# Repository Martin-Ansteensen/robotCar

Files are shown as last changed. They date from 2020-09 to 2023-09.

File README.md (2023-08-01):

# robotCar - Still in progress
A remote controlled robot car with a meccanum drivetrain.
The inspiration for this project was taken from the many First Tech Challenge (FTC) robots that use a meccanum wheel drivetrain with position tracking. The components used in FTC robots are quite expensive, and I wanted to design a low-cost version of these robots,

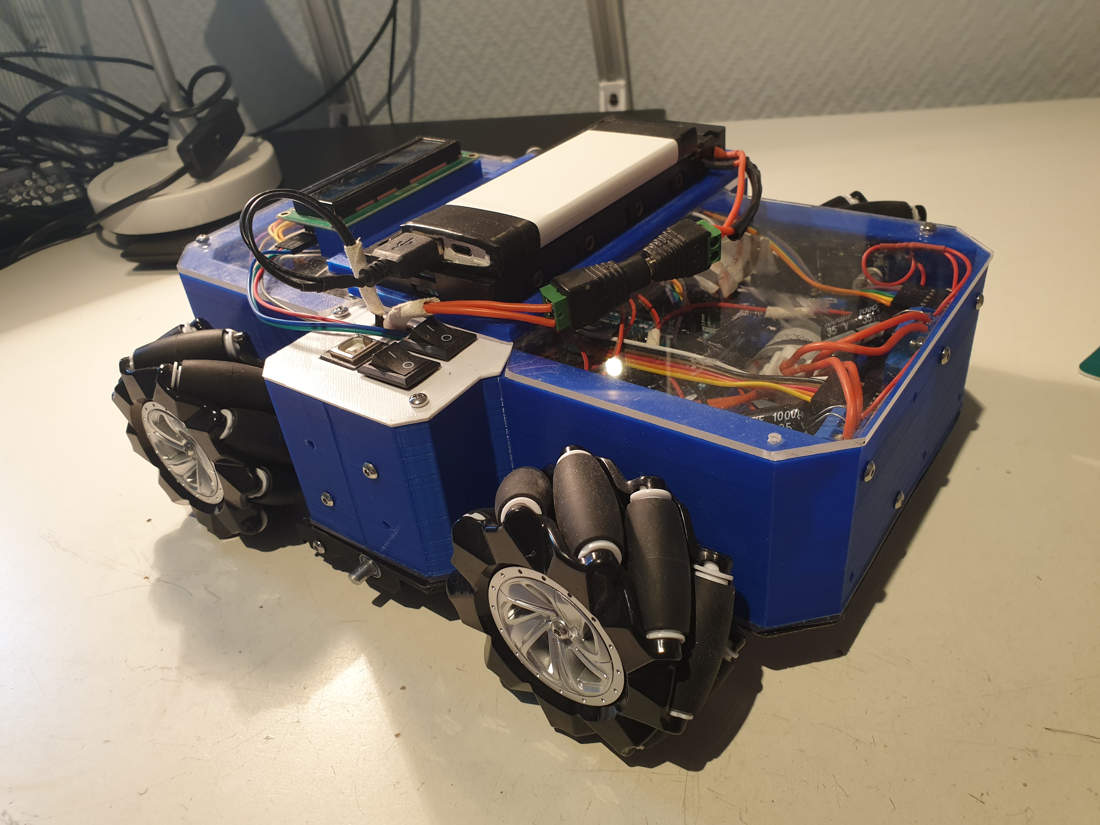
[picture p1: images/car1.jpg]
car


## Objectives
- [x] Meccanum drivetrain that enables the car to drive in all directions.
- [x] Remote control for the car.
- [x] Position tracking system consisting of 3 small omni wheels with encoders.
- [ ] PID-control for each axis of movement (x, y and rotation).
- [ ] Follow a path (predetermined in the program using some sort of a grid), using three omniwheels tracking the movement of the car.

## Design
### Meccanum drivetrain
A meccanum wheel consists of two disks with smaller wheels (rollers) attached in between them. The axis of the rollers are at 45° to the wheel plane and 45° to the axis perpendicular to the disks. A meccanum drivetraing consits of four meccanum wheels, each with it's own DC-motor. By adjusting the speed of each wheel, one can make the drivetrain move in any direction.
### Position tracking (used for odometry)
Tracking the car's position is not easily achieveable as the the meccanum wheels used for the drivetrain slips a lot, which removes the possibilty of using encoders on the drivetrain motors to track the position. Instead, three omni wheels (almost like meccanum wheels, but the axis of the rollers are parallel to the wheel plane), each with it's own rotary encoder is used. To ensure contact with the ground and avoid slipping, the omni wheels were mounted on a small platform with a rubber band forcing them into the ground. By constantly checking the change of the three encoders, the change in the robot's position can be found. 

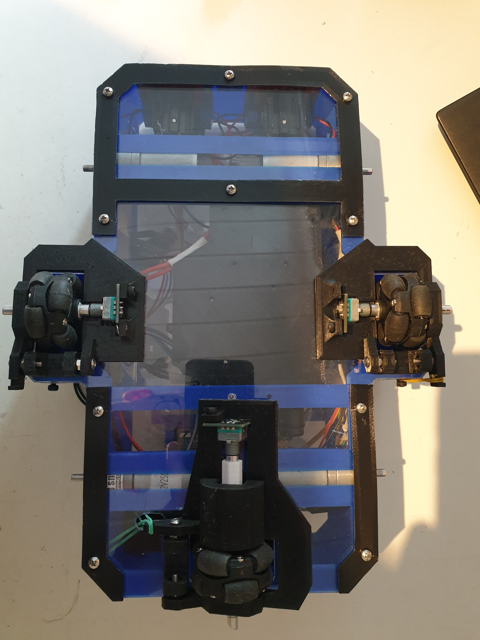
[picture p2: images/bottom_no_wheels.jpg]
bottom_no_wheels

bottom_with_wheels

Demo of the position tracking algorithm. Some error is present, as expected, but it is usable. The error is mainly caused by missed encoder-steps and the encoders low resolution (only 40 steps per revolution), causing accumulative error in the position caclulations.

Position tracking demo (https://www.youtube.com/watch?v=OhbFRzOGtvk)

### Electronics
- Gyro (mpu6050). Experimented with using motion data from the sensor to caculate changes in the position, but the data had to much jitter. Did work to keep track of orientation.
- Arduino Mega (main brain of car).
- Three Arduino Pro Minis (in an effort to detect all steps from the rotary encoder, each encoder was connected to it's own designated Arduino responsible for counting the steps of the encoder).
- Four DC-motors
- Two L298N Motor Drivers
- Battery pack (used by motors)
- Power bank (used by the other electronics to avoid voltage spikes caused by motors)
- Buck converter (transform voltage from power bank)
- LCD (display the position of the robot)
- Four KY-040 Rotary Encoders
- nrf24l01 (radio module)
- A miscellaneous collection of common components (wires, capacitors, switches)

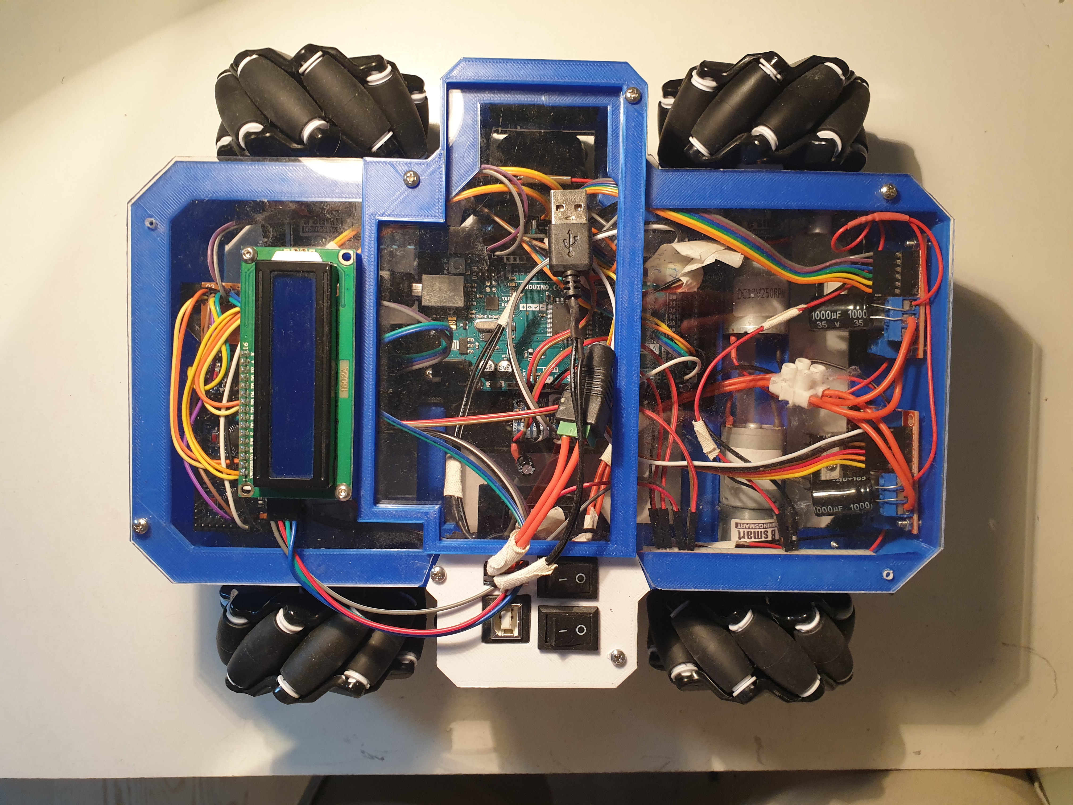
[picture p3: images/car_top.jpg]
car_top


## Remote control
Demo of the car being controlled by a remote control. It is using the position tracking combined with a PID-controller to keep the same orientation.

Remote control demo (https://www.youtube.com/watch?v=tdJjwmVsyyM)

## Path following
The interesting aspect of this project was to make it follow a path (a simple path: drive straight to the left for 10cm, 10cm forward, 10cm diagonally, or a more complex one: a circle, any mathematical curve). By interpolating through the path, using feedback from the position tracking to make sure the car drives to each sub-point on the path, one can ultimately follow any path.

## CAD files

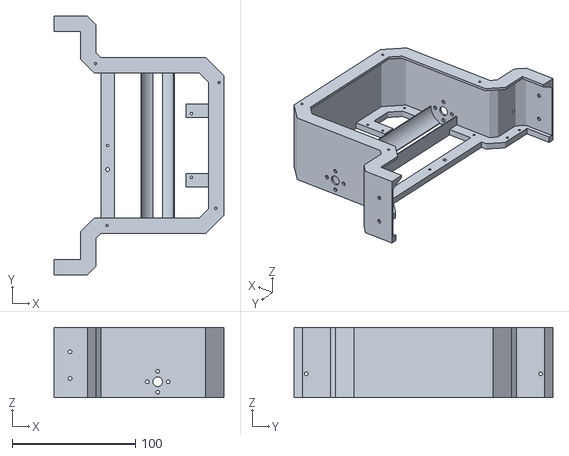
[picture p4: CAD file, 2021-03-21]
3d-model/backBody.stl
137.8 x 210.0 x 57.0

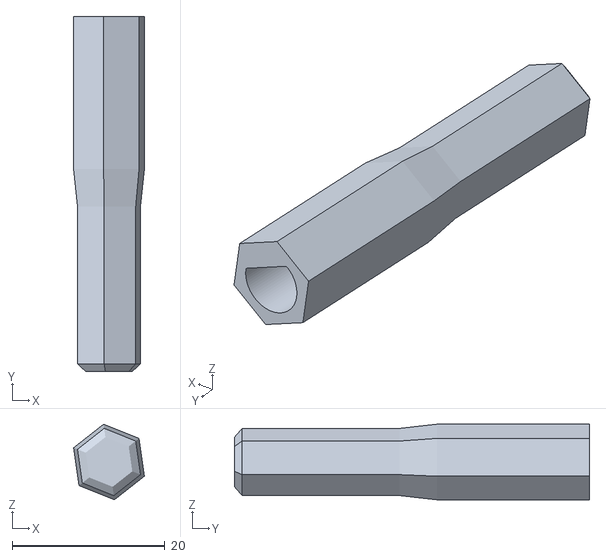
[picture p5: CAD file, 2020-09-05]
couplerLong.stl
9.28 x 46.5 x 9.90

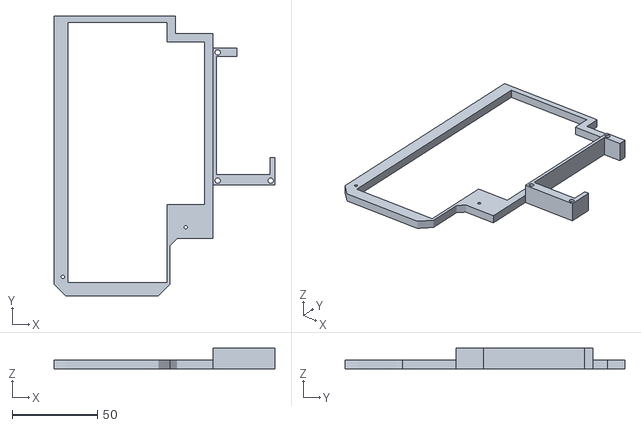
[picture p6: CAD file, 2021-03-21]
3d-model/batteryholder.stl
129.3 x 163.8 x 12.0

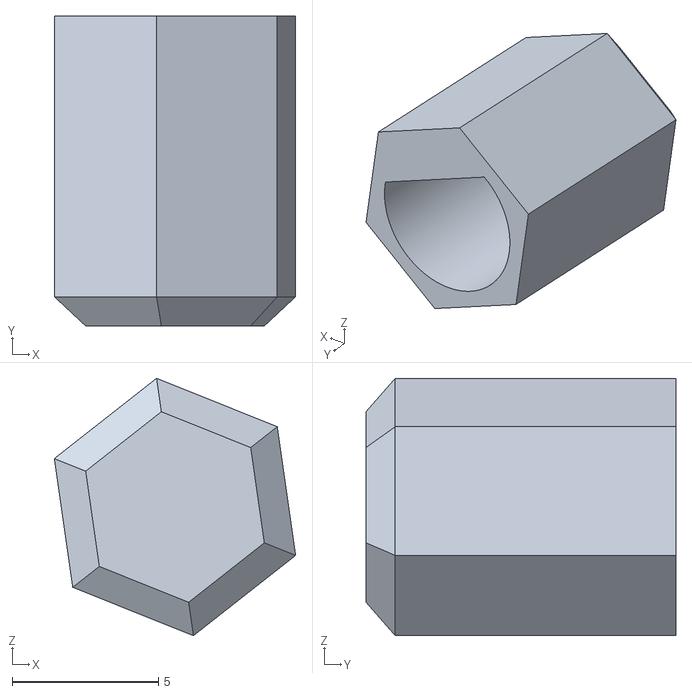
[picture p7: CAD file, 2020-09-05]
smallCoupler.stl
8.25 x 10.6 x 8.80

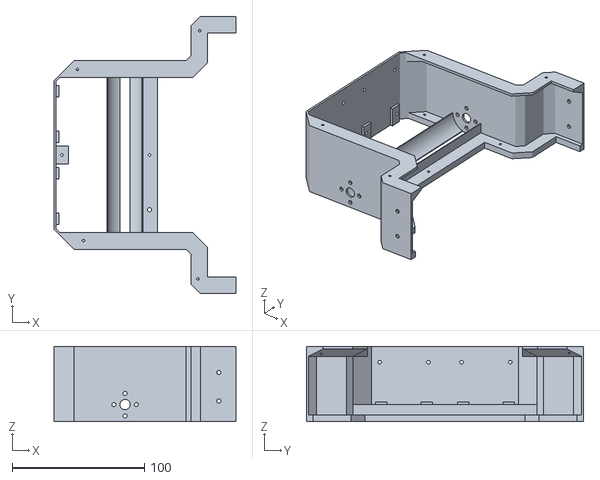
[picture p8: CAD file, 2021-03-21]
3d-model/frontBody.stl
137.8 x 210.0 x 57.0

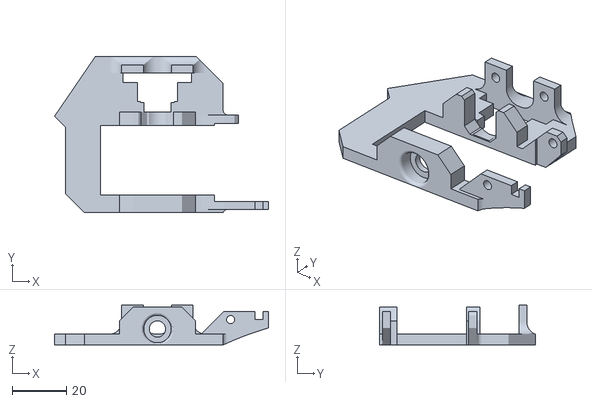
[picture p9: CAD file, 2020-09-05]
LeftOmni.stl
79.0 x 57.7 x 14.8

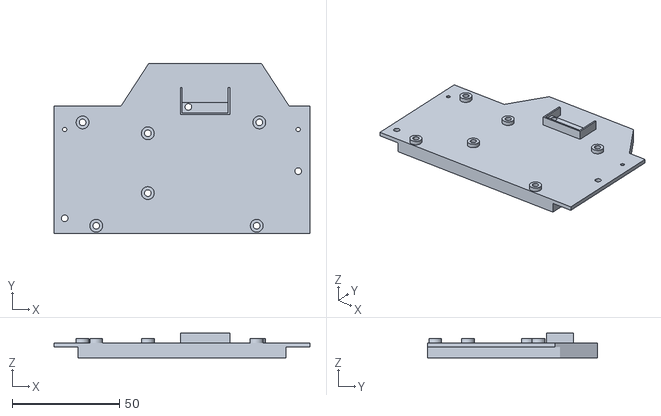
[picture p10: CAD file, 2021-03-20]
3d-model/electronicsplattform.stl
119.5 x 79.1 x 11.5

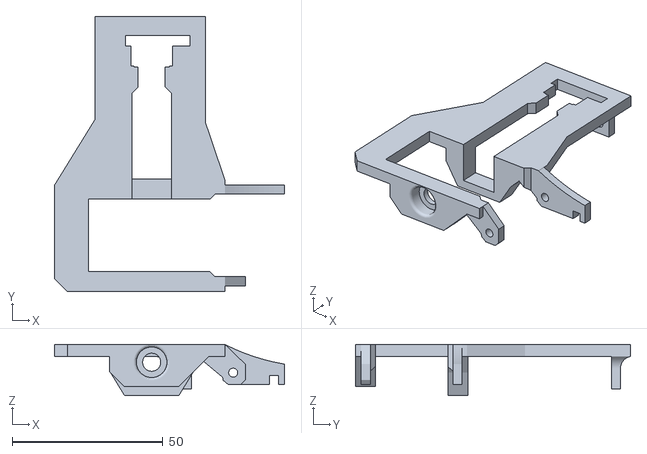
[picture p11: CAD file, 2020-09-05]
BackOmni.stl
76.2 x 91.1 x 16.9

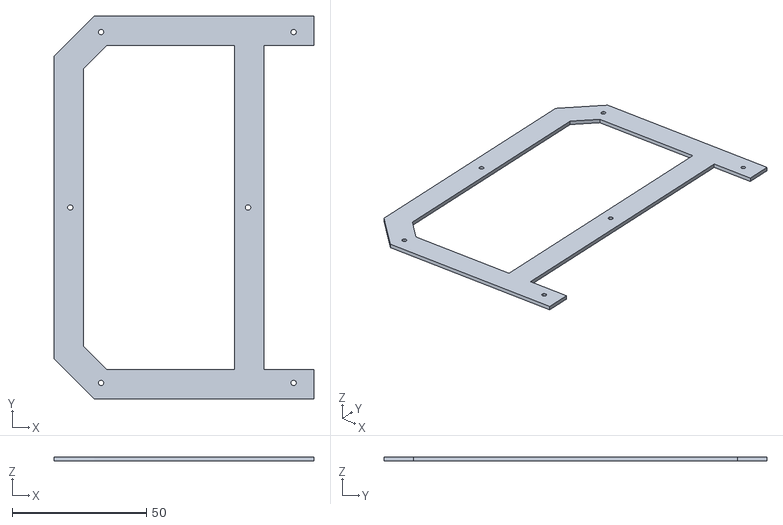
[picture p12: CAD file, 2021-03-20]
3d-model/spacer1.stl
96.8 x 142.8 x 1.60

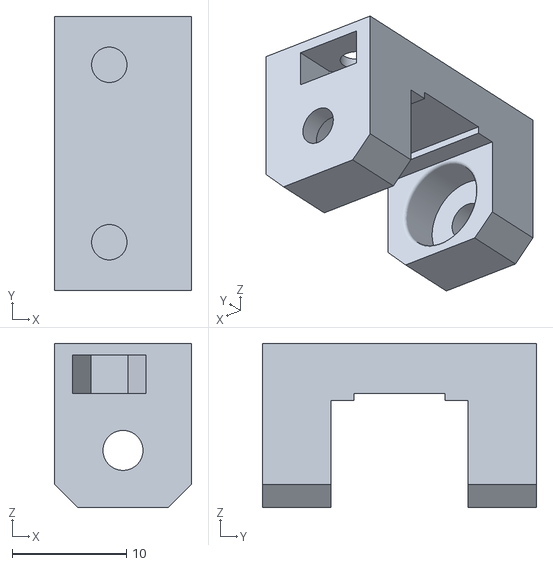
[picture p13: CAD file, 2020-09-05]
3.5Hinge.stl
12.0 x 24.0 x 14.4

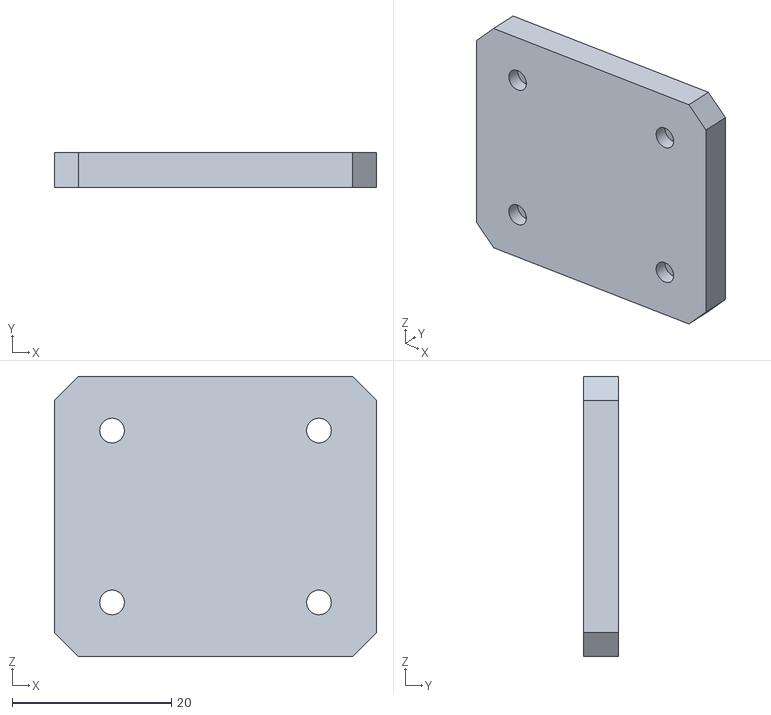
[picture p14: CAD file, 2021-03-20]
3d-model/sideCoupler.stl
40.5 x 4.40 x 35.2

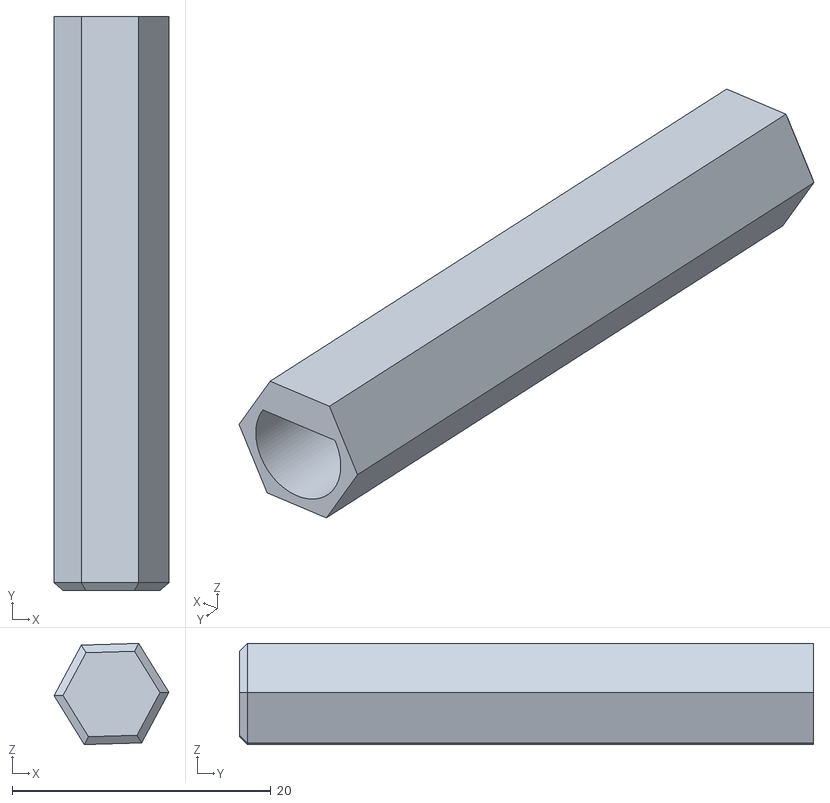
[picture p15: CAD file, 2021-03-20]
3d-model/longcouplr.stl
8.89 x 44.4 x 7.83

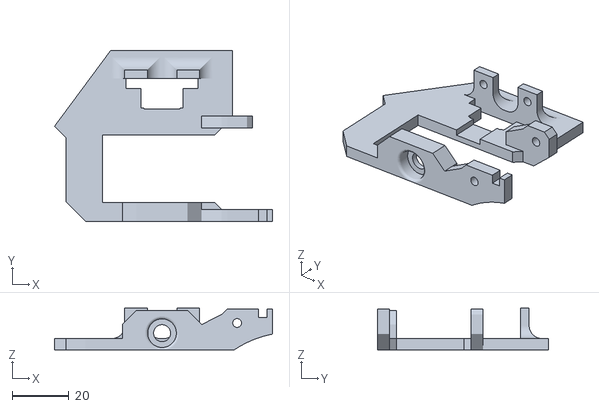
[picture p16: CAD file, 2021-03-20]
3d-model/rightencoder.stl
77.0 x 60.3 x 14.8

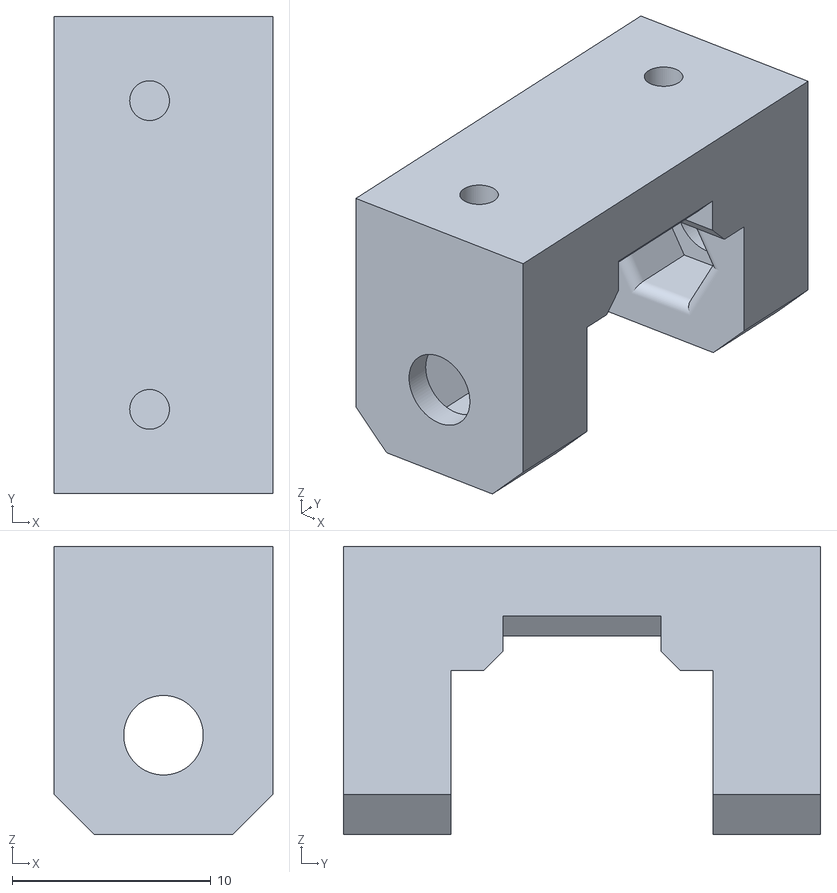
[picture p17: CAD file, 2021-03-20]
3d-model/hinge.stl
11.0 x 24.0 x 14.5

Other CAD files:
RightOmni.stl
3d-model/backencder.stl
3d-model/shortcoupler.stl
3d-model/spacer2.stl
3d-model/leftencoder.stl
3d-model/spacer3.stl

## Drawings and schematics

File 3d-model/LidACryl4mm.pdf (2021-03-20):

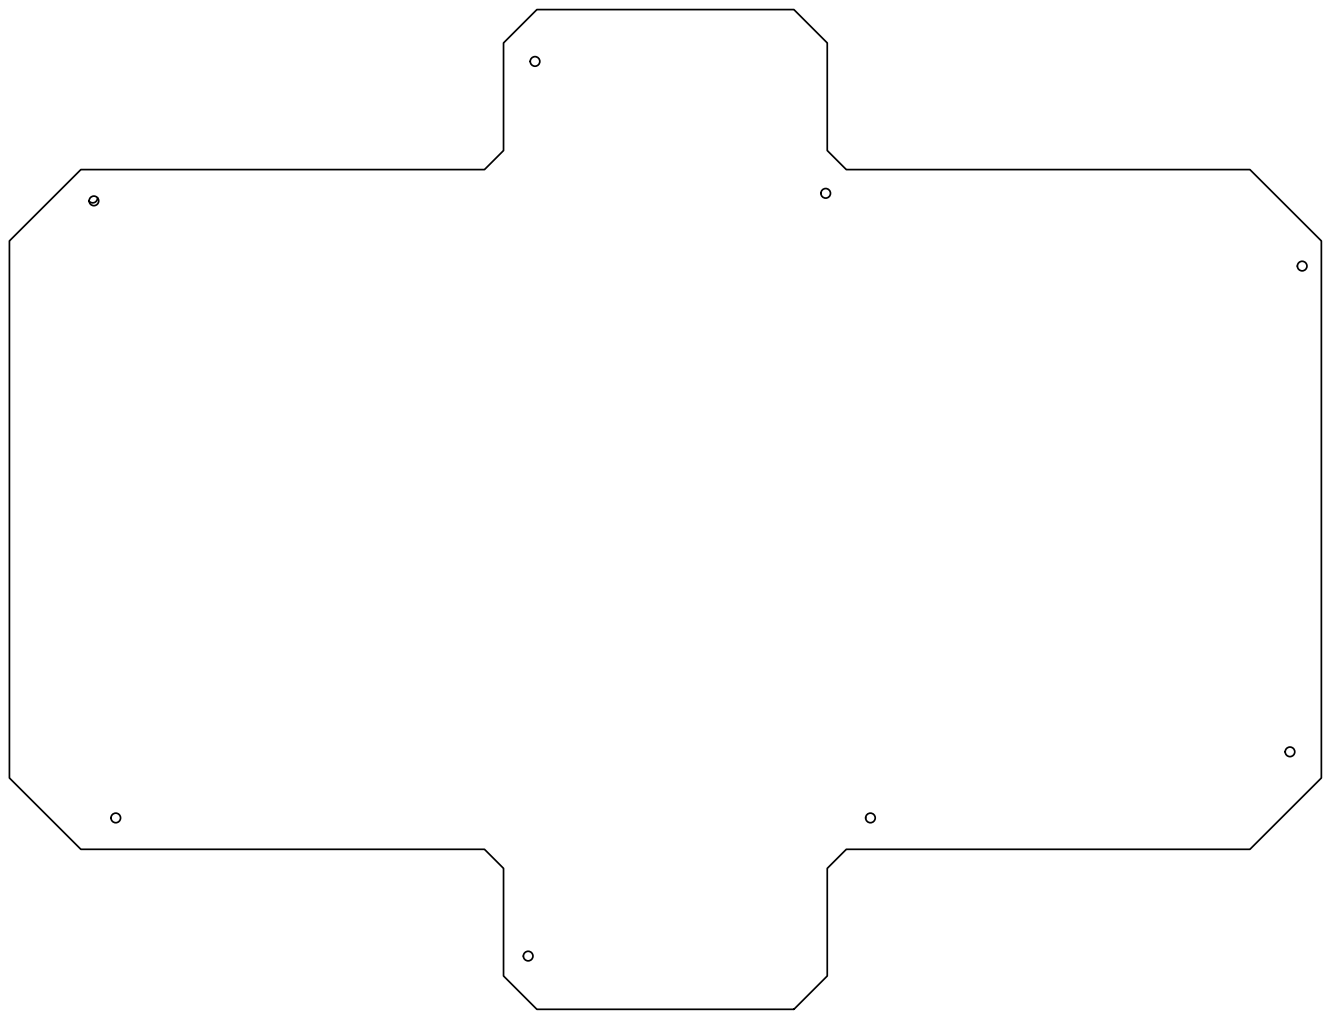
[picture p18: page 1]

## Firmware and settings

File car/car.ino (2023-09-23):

#include <LiquidCrystal_I2C.h>
#include <MPU6050_light.h>
#include "Wire.h"

#include <SPI.h>
#include <nRF24L01.h>
#include <RF24.h>


#include "encoder.h"
#include "navigation.h"
#include "motor.h"
#include "drivetrain.h"
#include "reciever.h"
#include "PID.h"

//  Connections from L298N to Arduino Mega

// Front left
#define enBLeft 7
#define in3Left 24
#define in4Left 22

//  Back left
#define enALeft 6
#define in1Left 28
#define in2Left 26


//  Front right
#define enARight 5
#define in1Right 25
#define in2Right 23

//  Back right
#define enBRight 4
#define in3Right 29
#define in4Right 27



unsigned long startMillis;  //some global variables available anywhere in the program
unsigned long currentMillis;
const unsigned long period = 1000;  //the value is a number of milliseconds

int leftChange, rightChange, normalChange;
double x = 0, y = 0, rotation = 0;
float error = 0;

float angle = 0;
int n = 0;
int mspeed = 125;
double inspeed, inangle;


LiquidCrystal_I2C lcd(0x3F, 16, 2); // Initialize LCD Display at address 0x27

EncoderUnit leftEncoder(I2C_LEFT_ENCODER_ADRESS);
EncoderUnit rightEncoder(I2C_RIGHT_ENCODER_ADRESS, -1);
EncoderUnit normalEncoder(I2C_NORMAL_ENCODER_ADRESS);

MPU6050 mpu(Wire);
Navigation navigate(mpu);

int MIN_VELOCITY = 35;
Motor frontLeftMotor(enBLeft, in3Left, in4Left, true, 0, MIN_VELOCITY);
Motor frontRightMotor(enARight, in1Right, in2Right, false, 0, MIN_VELOCITY);
Motor backLeftMotor(enALeft, in1Left, in2Left, false, 7, MIN_VELOCITY);
Motor backRightMotor(enBRight, in3Right, in4Right, true, 15, MIN_VELOCITY);

// TODO: TUNE PID-CONTROLLER
PID rotPID(150, 0.02, 500);
DriveTrain driveTrain(frontLeftMotor, frontRightMotor, backLeftMotor, backRightMotor, rotPID);

RF24 radio(49, 48);  // nRF24L01 (CE, CSN)
Reciever reciever(radio);


void setup() {
  Serial.begin(9600);
  Serial.println("Robotcar initializing");

  lcd.init();
  lcd.backlight(); // Turn on backlight

  leftEncoder.init();
  rightEncoder.init();
  normalEncoder.init();
  navigate.init();
  reciever.init();
  Serial.println("Robotcar finished initializing");
  startMillis = millis();  //initial start time


}

void displayPosition(double x, double y, double rotation) {
  // Top left corner
  lcd.setCursor(0, 0);
  lcd.print("x");
  lcd.setCursor(1, 0);
  lcd.print(x);

  // Top middel screen
  lcd.setCursor(8, 0);
  lcd.print("y");
  lcd.setCursor(9, 0);
  lcd.print(y);

  // Bottom left corner
  lcd.setCursor(0, 1);
  lcd.print("rot: ");
  lcd.setCursor(5, 1);
  lcd.print(rotation * 57.2957795131);
}

void loop() {

  leftEncoder.requestEncoderData();
  rightEncoder.requestEncoderData();
  normalEncoder.requestEncoderData();

  leftChange = leftEncoder.getEncoderChange();
  rightChange = rightEncoder.getEncoderChange();
  normalChange = normalEncoder.getEncoderChange();

  // Serial.print(leftChange);Serial.print(", ");Serial.print(rightChange);Serial.print(", ");Serial.println(normalChange);

  reciever.recieveData();
  reciever.processData();
  
  navigate.calculateNewPosition(leftChange, rightChange, normalChange);
  x = navigate.getXpos();
  y = navigate.getYpos();
  rotation = navigate.getOdometryOrientation();

  displayPosition(x, y, rotation);
  angle += reciever.getRotationChange();

  navigate.setOrientationTarget(angle);
  navigate.calculateOrientationError();
  error = navigate.getOrientationError();
  driveTrain.driveWithPID(reciever.getDriveMagnitude(), reciever.getDrive0(), error);
  Serial.print(error); Serial.print(", ");Serial.println(driveTrain.getCorrection());


}

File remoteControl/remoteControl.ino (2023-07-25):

#include <SPI.h>
#include <nRF24L01.h>
#include <RF24.h>


// Define the digital inputs
#define j1B_PIN 6  // Left joystick button
#define j1X_PIN A1 // Left joystick x axis
#define j1Y_PIN A0 // Left joystick y axis

#define j2B_PIN 9  // Right joystick button
#define j2X_PIN A2 // Rigth joystick x axis
#define j2Y_PIN A3 // Right joystick y axis

#define UP_PIN 2  // Up button
#define DOWN_PIN 5 // Down button
#define LEFT_PIN 3 // Left button
#define RIGHT_PIN 4  // Right button


#define POT_LEFT_PIN A4  // Left pot
#define POT_RIGHT_PIN A5 // Right pot

#define SWITCH_UP_PIN A7  // Switch up pin
#define SWITCH_DOWN_PIN A6 // Switch down pin


RF24 radio(7, 8);   // nRF24L01 (CE, CSN)
const byte address[6] = "00001"; // Radio-address

// Max size of this struct is 32 bytes - NRF24L01 buffer limit
struct Data_Package {
  byte j1PotX;
  byte j1PotY;
  byte j2PotX;
  byte j2PotY;
//  byte j1Button;
//  byte j2Button;
//  byte up;
//  byte down;
//  byte left;
//  byte right;
//  byte pot1;
//  byte pot2;
//  byte switch1;
//  byte switch2;
};
Data_Package data;

void setup() {
  Serial.begin(9600);
  Serial.println("Transmitter running");  
  // Start the radio broadcasting
  radio.begin();
  radio.openWritingPipe(address);
  radio.setAutoAck(false);
  //radio.setDataRate(RF24_250KBPS);
  radio.setPALevel(RF24_PA_MIN);
  
  // Activate the Arduino internal pull-up resistors
  pinMode(j1B_PIN, INPUT_PULLUP);
  pinMode(j2B_PIN, INPUT_PULLUP);
  
  pinMode(UP_PIN, INPUT_PULLUP);
  pinMode(DOWN_PIN, INPUT_PULLUP);
  pinMode(LEFT_PIN, INPUT_PULLUP);
  pinMode(RIGHT_PIN, INPUT_PULLUP);
}
void loop() {
  // Read all analog inputs and map them to one Byte value
  data.j1PotX = map(analogRead(j1X_PIN), 0, 1023, 0, 255);
  data.j1PotY = map(analogRead(j1Y_PIN), 0, 1023, 0, 255);
  
  data.j2PotX = map(analogRead(j2X_PIN), 0, 1023, 0, 255);
  data.j2PotY = map(analogRead(j2Y_PIN), 0, 1023, 0, 255);

//   data.pot1 = map(analogRead(POT_LEFT_PIN), 0, 1023, 0, 255);
//   data.pot2 = map(analogRead(POT_RIGHT_PIN), 0, 1023, 0, 255);
//
//   if (analogRead(SWITCH_UP_PIN) < 5){
//     data.switch1 = 0;
//     data.switch2 = 1;
//   } else if (analogRead(SWITCH_DOWN_PIN) < 5){
//     data.switch2 = 0;
//     data.switch1 = 1;
//   } else {
//     data.switch1 = 1;
//     data.switch2 = 1;
//   }


  // // Read all digital inputs
  // data.j1Button = digitalRead(j1B_PIN);
  // data.j2Button = digitalRead(j2B_PIN);

  // data.up = digitalRead(UP_PIN);
  // data.down = digitalRead(DOWN_PIN);
  // data.left = digitalRead(LEFT_PIN);
  // data.right = digitalRead(RIGHT_PIN);

  
  // Print data
   Serial.print(F("L_JOY XY: ")); Serial.print(data.j1PotX); Serial.print(F(" , ")); Serial.print(data.j1PotY); Serial.print(F(" , ")); 
  // Serial.print("L_B: "); Serial.print(data.j1Button); Serial.print(" , ");
   Serial.print(F("R_JOY XY:   ")); Serial.print(data.j2PotX); Serial.print(F(" , ")); Serial.print(data.j2PotY); Serial.print(F(" , "));
  // Serial.print("R_B:   "); Serial.print(data.j2Button); Serial.print(" , ");
  // Serial.print("UP: "); Serial.print(data.up); Serial.print(" , ");
  // Serial.print("DOWN: "); Serial.print(data.down); Serial.print(" , ");
  // Serial.print("LEFT: "); Serial.print(data.left); Serial.print(" , ");
  // Serial.print("RIGHT: "); Serial.print(data.right); Serial.print(" , ");
  // Serial.print("L_POT: "); Serial.print(data.pot1); Serial.print(" , "); 
  // Serial.print("R_POT: "); Serial.print(data.pot2); Serial.print(" , "); 
  // Serial.print("SW_FOR: "); Serial.print(data.switch1); Serial.print(" , "); 
  // Serial.print("SW_BAC: "); Serial.print(data.switch2); 
   Serial.println(); 

  // Send the whole data from the structure to the receiver
  radio.write(&data, sizeof(Data_Package));
}

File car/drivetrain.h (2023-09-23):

#ifndef _DriveTrain_h
#define _DriveTrain_h
#include "motor.h"
#include "PID.h"

// https://arduino.stackexchange.com/questions/24033/proper-use-of-and-when-passing-objects-in-methods

class DriveTrain {
    private:
        // Pointers to motor-objects
        Motor& frontLeft, frontRight, backLeft, backRight;
        double motorVelocities[4];
        float rot_correction;
        PID& rotPID;

    public:
        DriveTrain(Motor& _frontLeft, Motor& _frontRight, Motor& _backLeft, Motor& _backRight, PID& _rotPID) 
                  : frontLeft(_frontLeft), frontRight(_frontRight), backLeft(_backLeft), backRight(_backRight), rotPID(_rotPID) {
            init();
        }

        void init(){
        }

        void caculateVelocities(int motorSpeed, float angle){
            motorVelocities[0] = (motorSpeed*sin(angle+M_PI/4)*sqrt(2)); // Front left
            motorVelocities[1] = (motorSpeed*cos(angle+M_PI/4)*sqrt(2)); // Front right
            motorVelocities[2] = (motorSpeed*cos(angle+M_PI/4)*sqrt(2)); // Back left
            motorVelocities[3] = (motorSpeed*sin(angle+M_PI/4)*sqrt(2)); // Back right
        }

        void drive(int motorSpeed, float angle){
            caculateVelocities(motorSpeed, angle);
            frontLeft.drive(motorVelocities[0]);
            frontRight.drive(motorVelocities[1]);
            backLeft.drive(motorVelocities[2]);
            backRight.drive(motorVelocities[3]);
        }


        void scaleVelocities(){
            // Scales velocities so that none of them exceeds
            // 255 in magnitude
            double largest = abs(motorVelocities[0]);
            for (int i=1; i<4; i++){
                if(abs(motorVelocities[i]) > largest){
                    largest = abs(motorVelocities[i]);
                }
            }
            if (largest < 255){return;}
            // Only scale if the largest velocity exceeds 255 in magnitude
            for (int i=0; i<4; i++){
                motorVelocities[i] *= 255.0/largest;
            }
        }

        void driveWithPID(int motorSpeed, float angle, float error){
            rot_correction = rotPID.calculateCorrection(error);
            caculateVelocities(motorSpeed, angle);
            // Add error adjustment to velocities
            motorVelocities[0] += rot_correction;
            motorVelocities[1] -= rot_correction;
            motorVelocities[2] += rot_correction;
            motorVelocities[3] -= rot_correction;

            scaleVelocities();

            // Set motor velocities
            frontLeft.drive(motorVelocities[0]);
            frontRight.drive(motorVelocities[1]);
            backLeft.drive(motorVelocities[2]);
            backRight.drive(motorVelocities[3]);
        }

        void stop(){
            frontLeft.disable();
            frontRight.disable();
            backLeft.disable();
            backRight.disable();
        }

        float getCorrection(){
          return rot_correction;
        }
};
#endif

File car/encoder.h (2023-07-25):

#ifndef _EncoderUnit_h
#define _EncoderUnit_h
#include <Wire.h>

# define I2C_LEFT_ENCODER_ADRESS 10
# define I2C_RIGHT_ENCODER_ADRESS 11
# define I2C_NORMAL_ENCODER_ADRESS 12


class EncoderUnit {
  private:
    int I2Cadress;
    int encoderCount;
    int encoderChange;
    int dirMultiplier;
    volatile byte lowerByteCount, upperByteCount, lowerByteChange, upperByteChange;

  public:
    EncoderUnit(int I2Cadress, int directionMultiplier = 1) {
      this->I2Cadress = I2Cadress;
      this->dirMultiplier = directionMultiplier;
    }

    void init(){
      Serial.print(I2Cadress); Serial.println(F(" running"));
      Wire.begin();
    }

    void requestEncoderData() {
      Wire.requestFrom(I2Cadress, 4); 
      upperByteCount = Wire.read();  
      lowerByteCount = Wire.read(); 
      encoderCount = (int)upperByteCount << 8 | (int)lowerByteCount; 
      encoderCount = encoderCount*dirMultiplier;
       
      upperByteChange = Wire.read();
      lowerByteChange = Wire.read(); 
      encoderChange = (int)upperByteChange << 8 | (int)lowerByteChange;
      encoderChange = encoderChange*dirMultiplier;
    }

    int getEncoderChange() {
      return encoderChange;
    }

    int getEncoderCount() {
      return encoderCount;
    }
};
#endif

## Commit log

2020-08-04 working version with radio and PID
    [BackBody.stl, BackHinge.stl, BackOmni.stl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]
2020-08-06 Optical encoder
2020-09-05 first take at odometry
    [3.5Hinge.stl, BackBody.stl, BackHinge.stl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]
2020-09-06 Encoder continued
2020-09-13 Odometry working when not rotating
2020-09-26 Working odometry. Lacks precision
2020-09-30 Will implement interrupts
2020-09-30 Implemented interrupts- Doesn't work well
2021-03-20 Giving encoders a new go
    [3.5Hinge.stl, BackOmni.stl, LeftOmni.stl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]
2021-03-21 Added current version of 3d models
    [3.5Hinge.stl, BackOmni.stl, LeftOmni.stl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]
2021-04-24 Improved the odometry features
2023-07-20 Improved code to read encoders
2023-07-20 Implemented encoder-code from test-project into main project
2023-07-25 V2 software
    Updated the entire software to make it more clear and easier to work with. The new encoder code allows me to use the odometry encoders for rotation (has replaced the MPU6050) and position (which did not work before).
    [arduinoEncoderCounter.ino, car.ino, drivetrain.h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]
2023-09-23 New PID-script, updated lcd-code
    Implemented seperate PID-script. Updated lcd-code to match newest version of LiquidCrystel_I2C
